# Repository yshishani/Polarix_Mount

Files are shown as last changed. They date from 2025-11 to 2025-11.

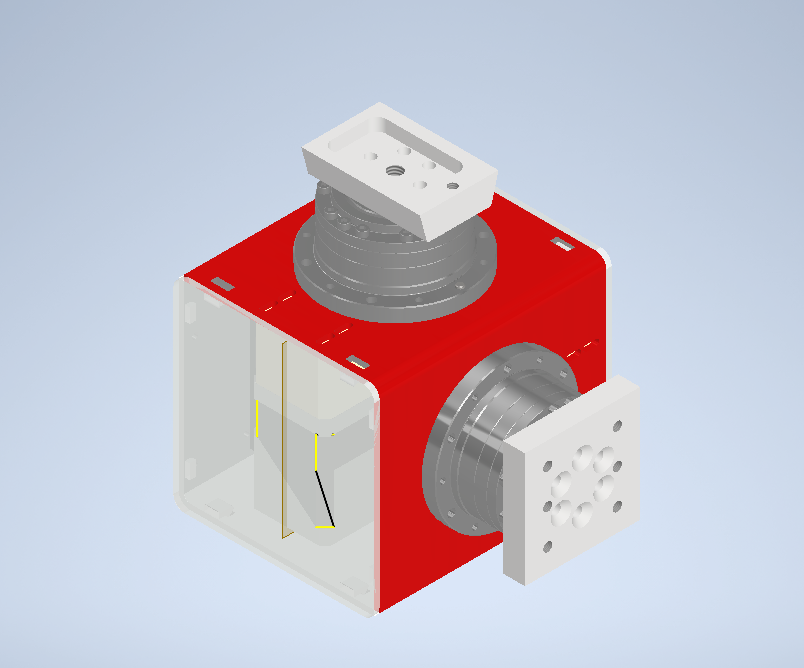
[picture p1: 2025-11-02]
Polarix Mount Design.png

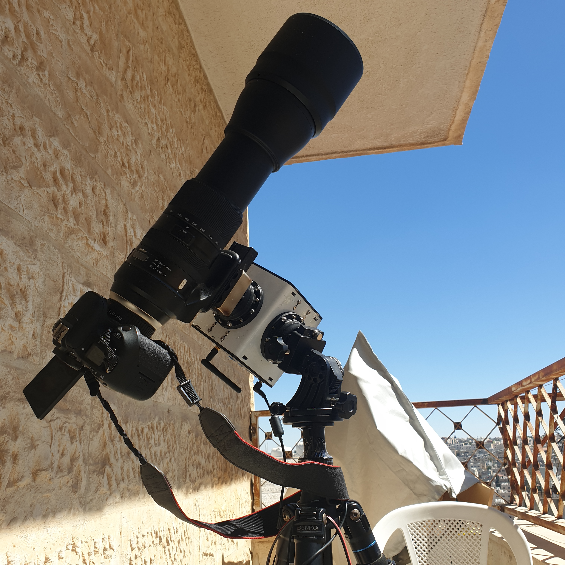
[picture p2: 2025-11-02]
Images/20250904_104644.jpg

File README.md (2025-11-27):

# Polarix Harmonic Drive Mount

I am sharing my designs and data for my DIY Harmonic Drive mount that I designed and manufactured locally in Amman Jordan.
This mount is much cheaper than if purchased as a ready made from China of any brand for a similar payload.

Total cost for me for the parts was around 375JOD, which is equivalent to around 530USD. The extra cost was due to our local customs and duties which were extremely overexaggerated by the customs officer who claimed that the parts like the FYSETC E4 and the 0.9deg NEMA 17 Motors are solely designated for 3D printers and we have a "non-just" law here in Jordan that all 3D printers and their (PARTS) must have prior authorization from the ministry of interior which took too much time and cost.

The mount is designed with rated load of 15kg without counterweight, and around 20kg with counterweight.

The firmware is based on open-source project OnstepX firmware, which is computerized telescope control system designed to give GoTo (computerized tracking) capabilities to a variety of telescope mounts.

I have uploaded the designs which were done using Autodesk Inventor 2025 Pro to the folder Inventor.

Parts list is also uploaded in the relevant folder.

I have upload a video to YouTube showing the full assembly process 

link: https://youtu.be/akRYA4y\_P54?si=YTsm9m11TzZYfvIg

Special thanks to Mountzilla, AlkaidMount, Astrophilos projects owners and many others for inspiring me to do my own mount.

By

Yousef Shishani

Amman - Jordan

2025

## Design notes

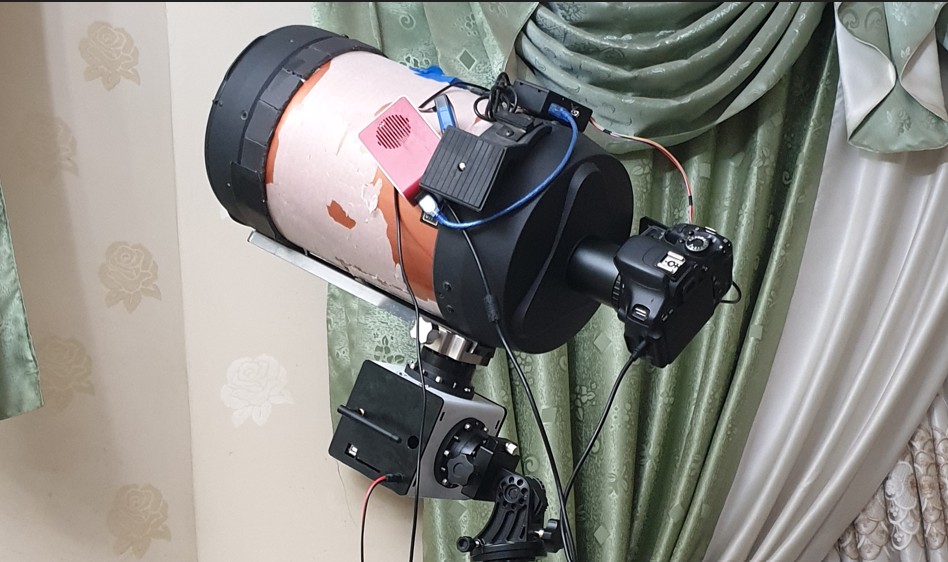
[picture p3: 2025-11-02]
Images/mount with telescope.jpg

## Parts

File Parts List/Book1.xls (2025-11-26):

Polarix Mount
Parts List
Item | Description | Quantity | Price | Notes
1 | Harmonic Drive HBS17 or CSG/CSF17 with 8mm input shaft bore size | 2
2 | NEMA 17 Motor 60mm for RA (either 1.8deg or 0.9deg) | 1 |  | As per the required resotution
3 | NEMA 17 Motor 40mm for DEC (either 1.8deg or 0.9deg) | 1 |  | As per the required resotution
4 | FYSETC E4 Board | 1
5 | GT2 16t 6mm Pulley 6mm width, 5mm borehole | 1
6 | GT2 60t (or 80t) for Harmonic Drive 6mm width, 8mm borehole | 1 |  | Can get higher gear ration with 80t and thus more torque and more resolution
7 | GT2 6mm Belt (158mm with 60t pulley) (or 186~188mm for 80t pulley) | 2
8 | 8mm Steel Shaft 50~55mm length | 2
9 | Steel Sheet 3mm for the Housing as per the two drawings cut & bent | 2
10 | Wedge for Telescope with Dovetail at least 43mm width | 1
11 | Dovetail Clamp 43mm | 1
12 | 3D printed material as per the stl files | 1
13 | 12~24 Volt powersupply. Can use a laptop power supply with around 18~19V output to the mount
14 | M3x40 Chease head screws | 4
15 | M3x16 Chease head screws | 16
16 | Cap Hex head screw M5x12 | 6
17 | C/S Screw M5x18 | 6
18 | Chease Head Screw M4x16 | 32
19 | Hex Nut M4 | 16
20 | Hex Nut M3 | 8

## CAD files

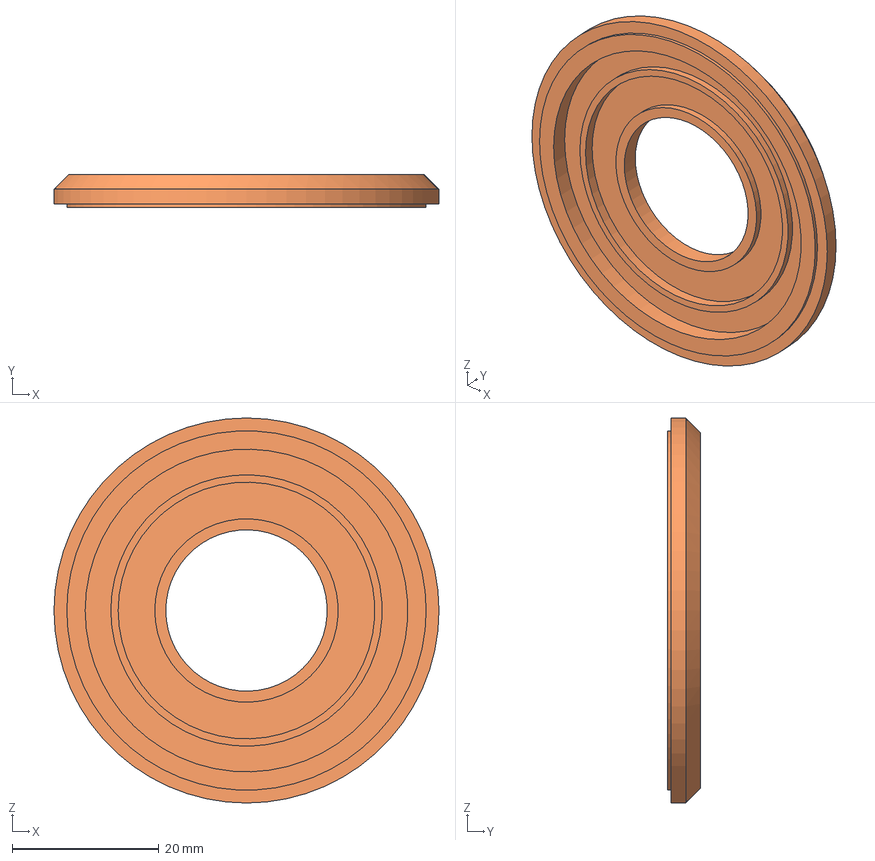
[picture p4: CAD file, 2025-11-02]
Inventor Files/3D Printing/Grease retainer disk.stp
52.5 x 4.50 x 52.5 mm

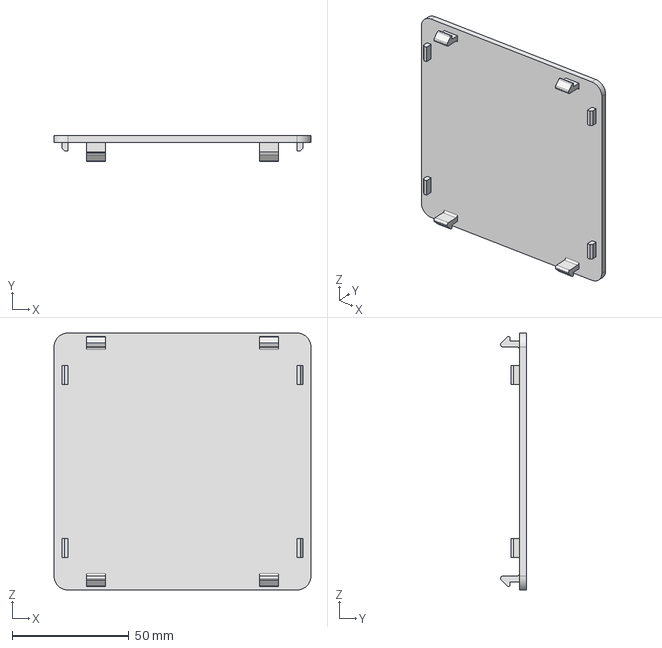
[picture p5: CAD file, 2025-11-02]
Inventor Files/3D Printing/Cover side-2.stp
110.0 x 11.1 x 110.0 mm

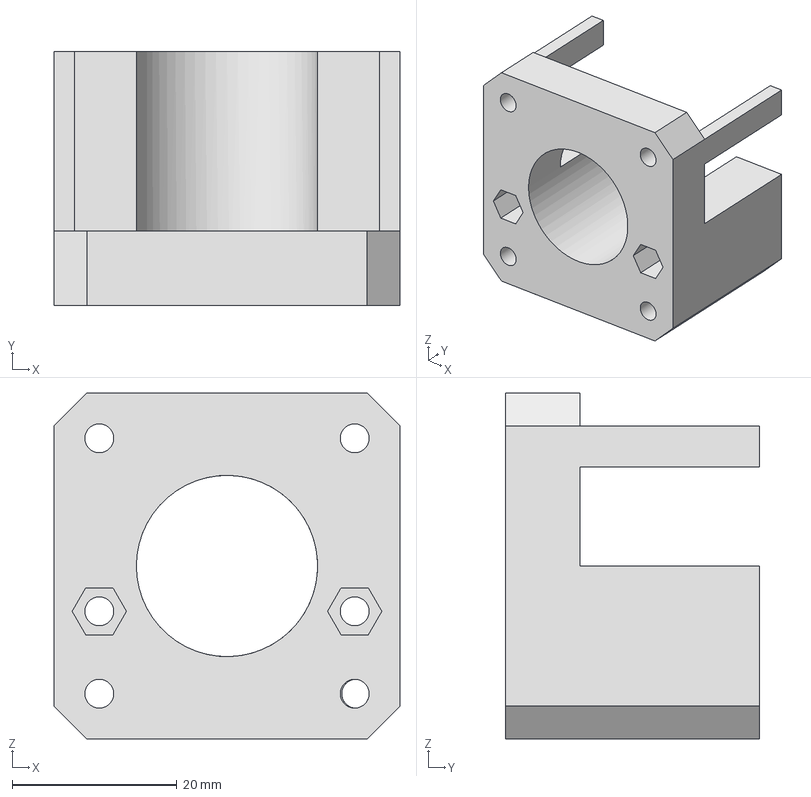
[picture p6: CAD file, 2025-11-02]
Inventor Files/3D Printing/Base for NEMA17.stp
42.0 x 30.8 x 42.0 mm

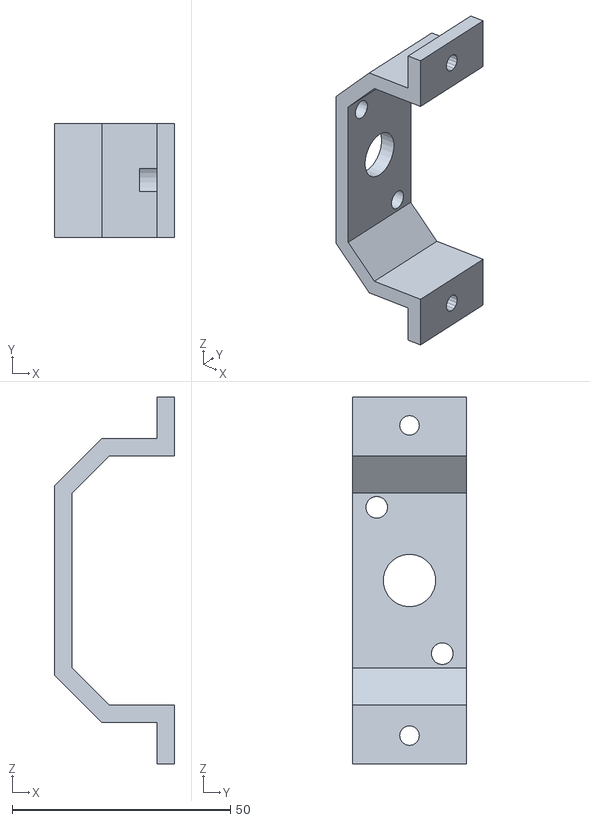
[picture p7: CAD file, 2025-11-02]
Inventor Files/3D Printing/Pulley Bearing Support.-3.stl
27.5 x 26.0 x 84.0

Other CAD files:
Inventor Files/Harmonic Mount Box Assembly.dwg
Inventor Files/DXF-For Laser Cutting/Face with Harmonic Drive-Unfolded.dwg
Inventor Files/Face with CWT hole.dwg
Inventor Files/DXF-For Laser Cutting/Face with CWT hole-Unfolded.dwg
Inventor Files/Face with Harmonic Drive.dwg
Inventor Files/3D Printing/Cover-USB side.stp
Inventor Files/Face with Harmonic Drive-Unfolded.dwg
Inventor Files/Face with CWT hole-Unfolded.dwg
Inventor Files/3D Printing/Base for NEMA17.stl
Inventor Files/3D Printing/Cover side-2.stl
Inventor Files/3D Printing/Cover-USB side.stl
Inventor Files/3D Printing/Grease retainer disk.ipt
Inventor Files/3D Printing/Grease retainer disk.stl
Inventor Files/Adapter plate for tube dovetail bracket-Optional.ipt
Inventor Files/Base for NEMA17.ipt
Inventor Files/Bearing.ipt
Inventor Files/CSF-17-XXX-2UH.iam
Inventor Files/Cover side-2.ipt
Inventor Files/Cover-USB side.ipt
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

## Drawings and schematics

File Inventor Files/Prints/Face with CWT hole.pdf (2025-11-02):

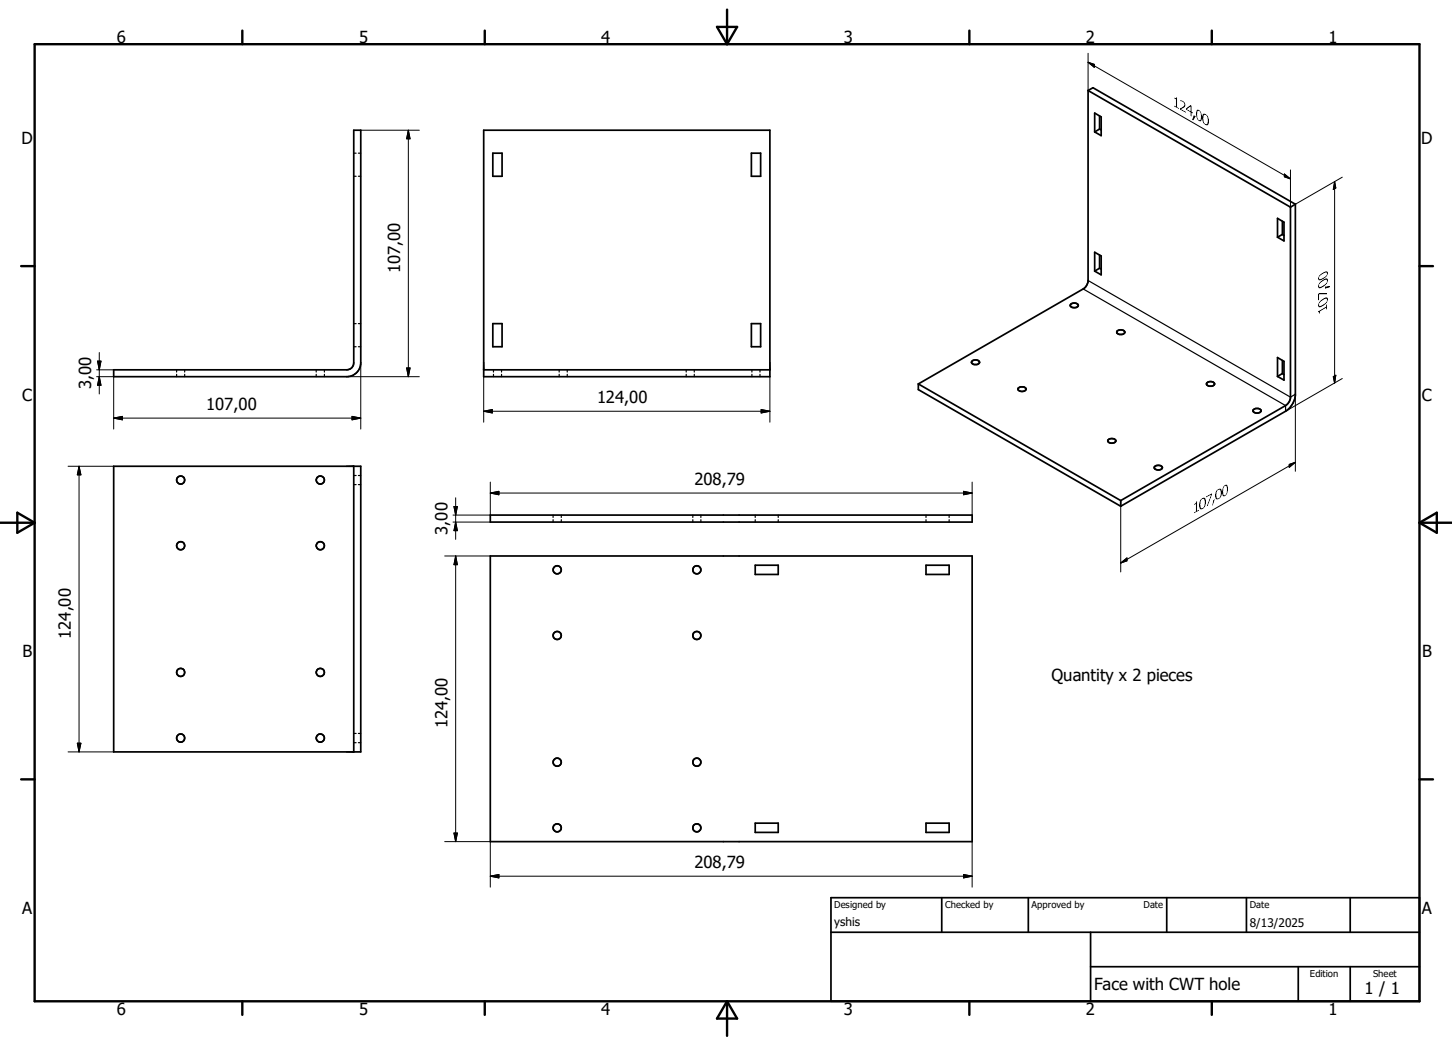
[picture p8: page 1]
yshis; Designed by; Checked by; Approved by; Date; 1 / 1 Edition; Sheet Date; Quantity x 2 pieces 124,00

Face with CWT hole

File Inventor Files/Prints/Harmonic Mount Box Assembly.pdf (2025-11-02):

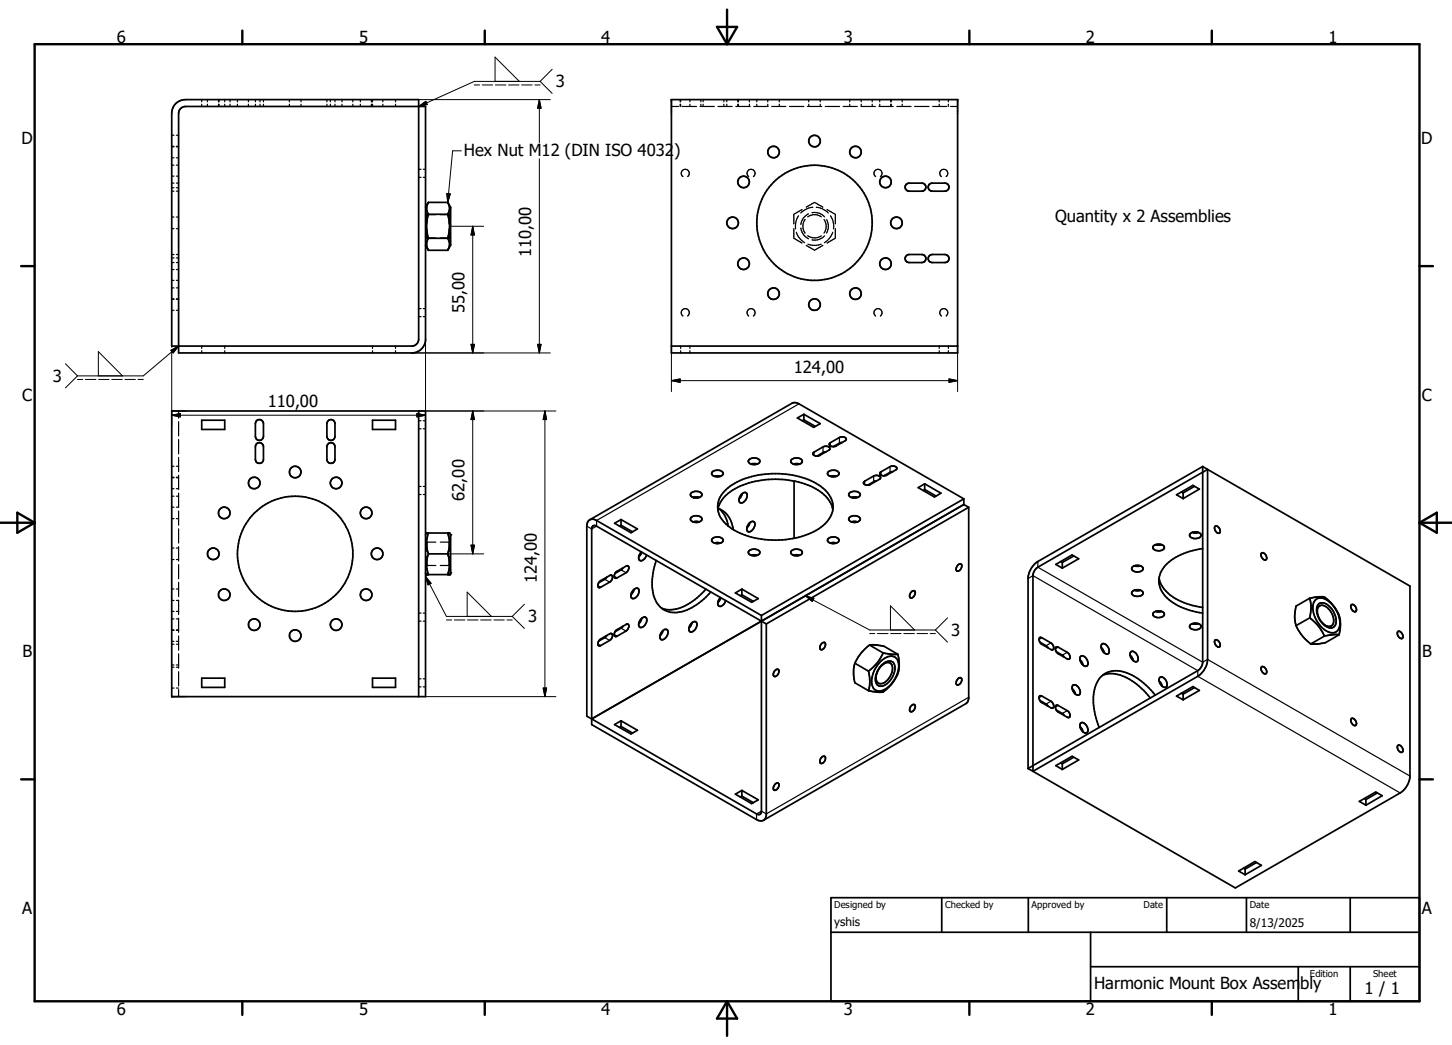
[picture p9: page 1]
yshis; Designed by; Checked by; Approved by; Date; 1 / 1 Edition; Sheet Date; Quantity x 2 Assemblies

Hex Nut M12 (DIN ISO 4032)

Harmonic Mount Box Assembly

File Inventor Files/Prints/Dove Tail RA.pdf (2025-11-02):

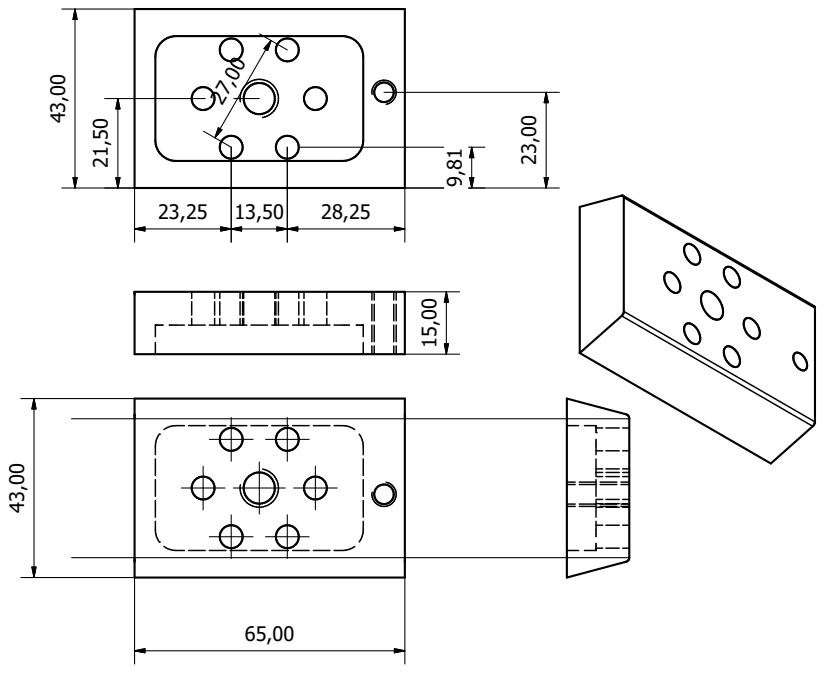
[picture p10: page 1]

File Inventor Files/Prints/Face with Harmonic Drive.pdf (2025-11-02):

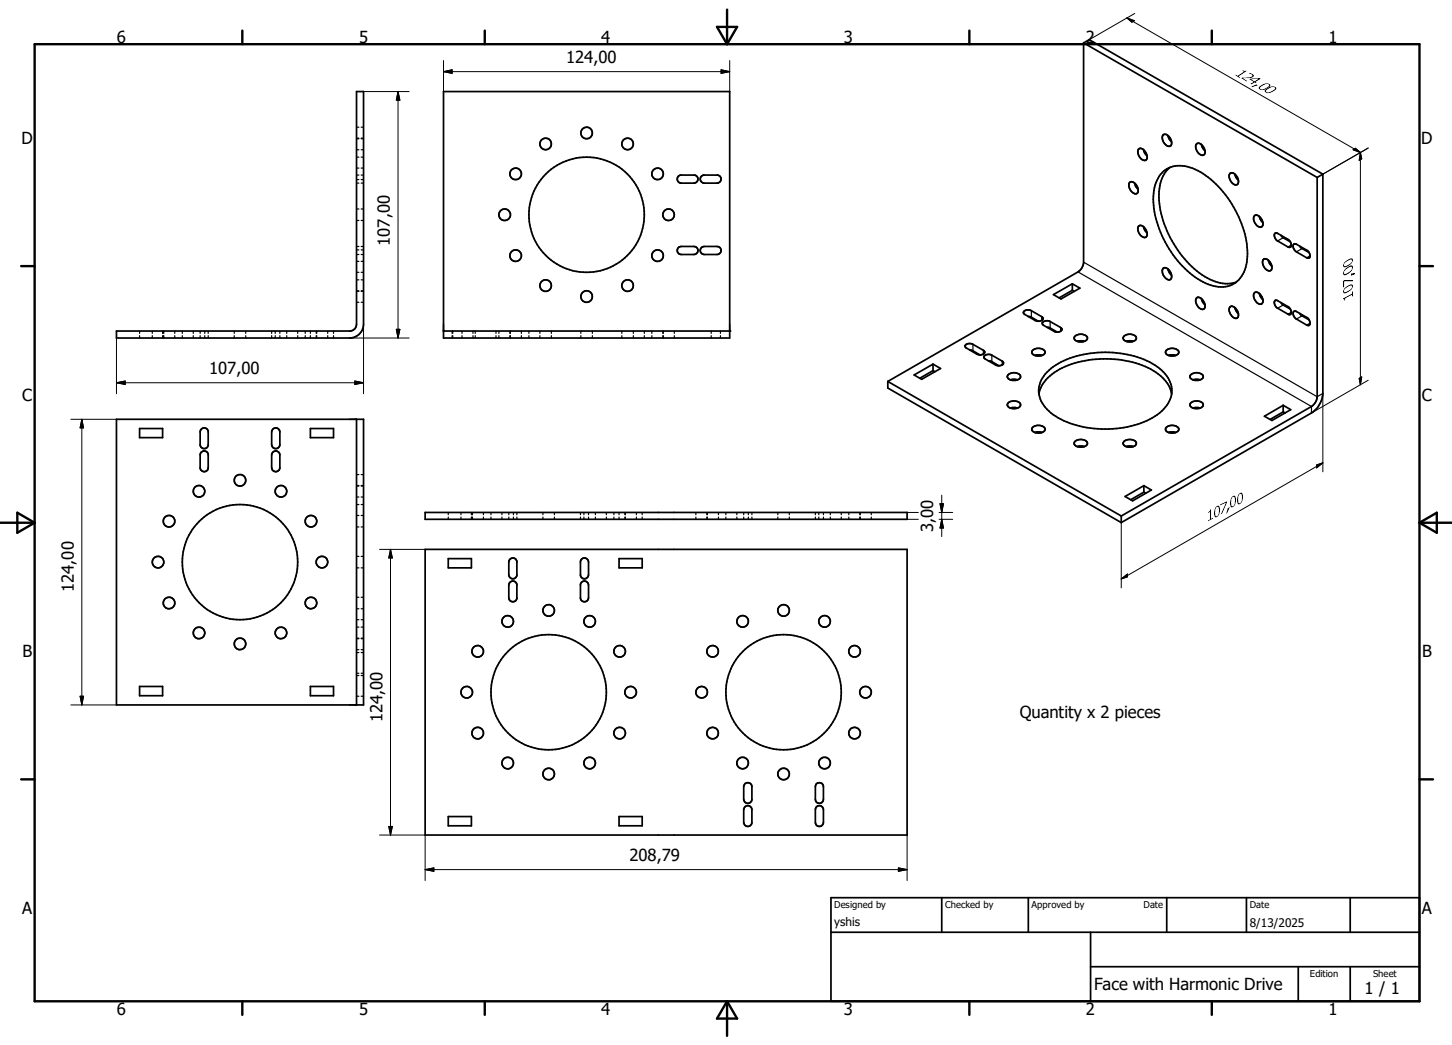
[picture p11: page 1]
yshis; Designed by; Checked by; Approved by; Date; 1 / 1 Edition; Sheet Date; 208,79 ¹²⁴,00; Quantity x 2 pieces

Face with Harmonic Drive

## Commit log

2025-11-02 Inventor files uploaded
    [Adapter plate for tube dovetail bracket-Optional.ipt, Base for NEMA17.ipt, Base for NEMA17.stl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]
2025-11-26 New folder with parts list uploaded and readme file updated
    [Book1.xls, CSF-17-XXX-2UH.0013.iam, Polarix Harmonic Mount Complete Assembly.0095.iam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]
